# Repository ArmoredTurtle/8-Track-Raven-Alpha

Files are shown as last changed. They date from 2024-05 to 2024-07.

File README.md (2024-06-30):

8-Track Raven 4 spool automated filament changer.

V0.0.41

Join our discord server here:

Join me on Discord (https://discord.gg/eT8zc3bvPR)

## Intro

This is an alpha version of the 8-Track project.
8-Track is a modular automated filament changer that is scaleable and compatible with any KLIPPER 3d printer.
Specifically 8-Track Raven's purpose is to do public testing of critical components at a lower price point.
Raven retains the same cassettes as the 8-Track while simplifying the hub and uses an off the shelf MCU.

## Objectives
The goal of alpha testing this project is to refine the cassettes as much as possible and prove reliability of the system.
Features like active filament drying are being worked on but do not currently have a timeline.

## Compatibility
Almost everything is subject to change unless specified as set in stone such as:
Cassette dimensions, 8-Track Raven frame.

# Raven BOM (Bill of Materials)

## Frame
| Qty | Item |
|-----|---|
| 4 | 412.5 2020 extrusions |
| 2 | 304.5 2020 extrusions |
| 2 | 219mm extrusions |
| 8 | M5x25 BHCS |
| 2 | M5x8 BHCS |
| 2 | M5 Roll Nuts |

## Hardware
| Qty | Item |
|-----|---|
| 4 | B-side cassete PCBs |
| 56  | M3x5 Heat set inserts |
| 16  | 0.5x5x15 Coil Springs |
| 16  | M3x20 FHCS |
| 32  | M3x12 SHCS |
| 32  | M5 Roll nuts |
| 32  | M5x10 BHCS |
| 11  | ECAS04 (remove rubber spacer) |

## Printed Parts
| Qty | Part Name |
|---|---|
| 1 - 4  | Backer_X |
| 4 | Backer_PCB_Spring_Plate_x4 |
| 1-4 | Drop_Plate_X |
| 1 | Mid_Plate_Lower |
| 1 | Mid_Plate_Upper |
| 1 | 6-1_Hub |
| 1 | BTT_MMB_CAN_Mount |

# Cassette BOM ((Bill of Materials)  Per Cassette)

## Electronics
| Qty | Item |
|-----|---|
| 1 | 20mm Nema 17 motor |
| 1 | Endstop microswitch (Omron D2F) |
| 1 | mg 996r servo |
| 1 | Cassette Side-A PCB |

## Hardware
|  Qty  | Item |
|---|---|
|  21 | M3x6 SHCS |
|  6 | M3x8 SHCS |
|  7 | M3x20 SHCS |
|  3 | M3x20 FHCS |
|  6 | M3 Washer |
|  20 | M3x5 Heat set inserts |
|  1 | BMG Extruder gear kit |
|  1 | Spring (6mm OD, 1mm Wire Size, 7.5mm Compressed Length, 15mm Free Length, 37.2N Load Capacity) |
|  2 | #211 Orings (13/16" ID, 1 1/16" OD) |
|  4 | 608 Bearings |
|  1 | R4zz Bearing OR 634ZZ (print tension arms) |
|  2 | 80x8mm Shaft |
|  1 | HF081412 one way bearing (8mm ID, 14mm OD, 12mm L) |
|  1 | 5mm Steel ball bearing |
| ~32mm | 4mm OD 3mm ID bowden tube |
|  4 | 6x3mm magnets |
|  1 | 0.5x5x15 Coil Spring |
| *** | If split cassette +1 M3x6 SHCS, +1 M3X5 heat set insert |

## Printed Parts
| Qty | Item |
|-----|---|
| 1 | Cassette Lid |
| 1 | Cassette Shell |
| 1 | Frane |
| 1 | Idler Frame |
| 1 | TensionArm_Upper |
| 1 | TensionArm_Lower |
| 2 | Idler Roller |
| 2 | Idler Spacer |
| 2 | Inner Roller |
| 2 | Roller_TPU95A |

*Insert lots more reading material here *later**

[Buy me a coffee to help keep this project going!](https://buymeacoffee.com/armoredturtle)

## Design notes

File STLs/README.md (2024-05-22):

# Print Settings
All parts should be printed in these settings unless specifically called out here as otherwise.

| Setting 	| Value 	|
|---	|---	|
| Nozzle 	| 0.4mm 	|
| Layer Height 	| 0.2mm 	|
| Perimeters/Walls 	| 4 	|
| Bottom Layers 	| 4 	|
| Top Layers 	| 4 (0.8mm) 	|
| Infil Density 	| 15 	|
| Infil Pattern 	| Gyroid 	|

## Material choice
PLA, PETG and ABS have been tested, all work however PETG is not recommended for extruder parts or drop plates.
When using heated inserts, be sure to use appropriate temperatures for your selected material.

## Part call out!
Guidler: same settings with 6 perimeters and 40% infill

Servo_Arm: Same as guidler unless pla. If in PLA print at 100% infill.

6-1Hub: Increase infill to 20% to ensure proper support of filament paths.

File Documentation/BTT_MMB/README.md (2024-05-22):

# BTT MMB CAN Board

Full information on the BTT MMB CAN board can be found here:
https://github.com/bigtreetech/MMB

# Details
This project requires use of four independently controllable servo motors.

When controlling these via an STM32 or similar micro controller, it is mandatory to use an ADC pin.

There are four accessible ADC pins on this board:

PA0 PA1 PA3 PA4

These will be used in the config for the servos. If you use a different pin your servo will not work.

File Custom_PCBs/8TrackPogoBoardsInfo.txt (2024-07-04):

The 5V port on these boards is intended for future shenanigans and does not need to be hooked to anything.
It is common to the 5V and GND going to the servo.

Identification: There is A-Side and B-Side, you can identify this by the side that the JST connectors are on, not the side that the pogo is on.
B-side boards have the male pogos and go on your hub (raven or other) A-side boards have the female pogos and are for the cassettes. 

The pogo pins can be sourced here, you want the 8-pin NO EAR variation.
https://www.aliexpress.us/item/3256805938998871.html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
Each pair uses 2 4 pin JST-XH connectors, 2 3 pin, 4 2 pin.

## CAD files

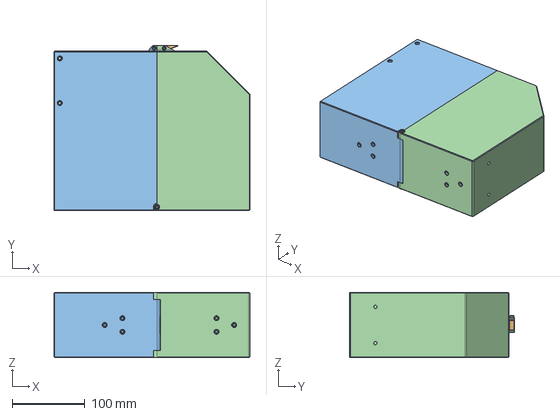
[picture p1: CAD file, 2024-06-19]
CAD/Split_Cassette_Bottom_Hinge v2.step
270.1 x 228.0 x 90.0 mm
M3x20 SHCS x 4

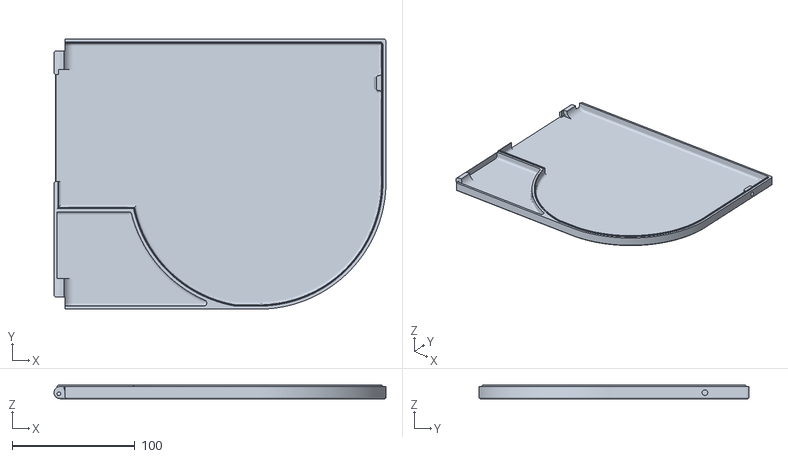
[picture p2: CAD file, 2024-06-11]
STLs/Cassette/Cassette_Lid.stl
270.2 x 220.0 x 11.0

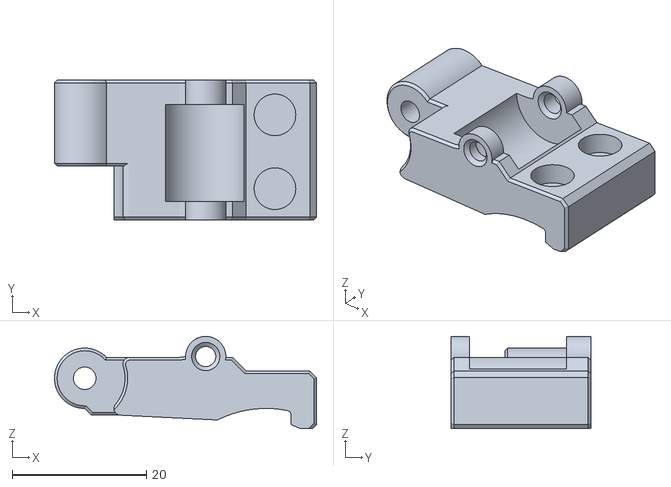
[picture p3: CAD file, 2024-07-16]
STLs/Cassette/Extruder_Module_V2/Thickened Guidler.stl
39.0 x 20.8 x 13.7

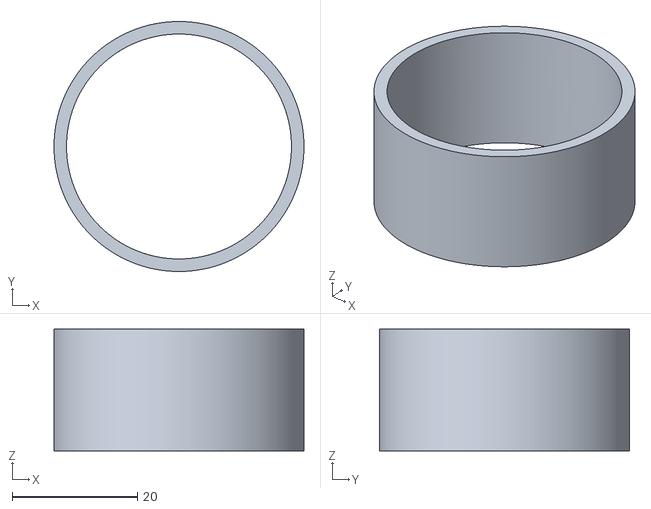
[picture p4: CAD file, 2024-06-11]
STLs/Cassette/Respooler/Roller_TPU95A_x2.stl
39.8 x 39.8 x 19.4

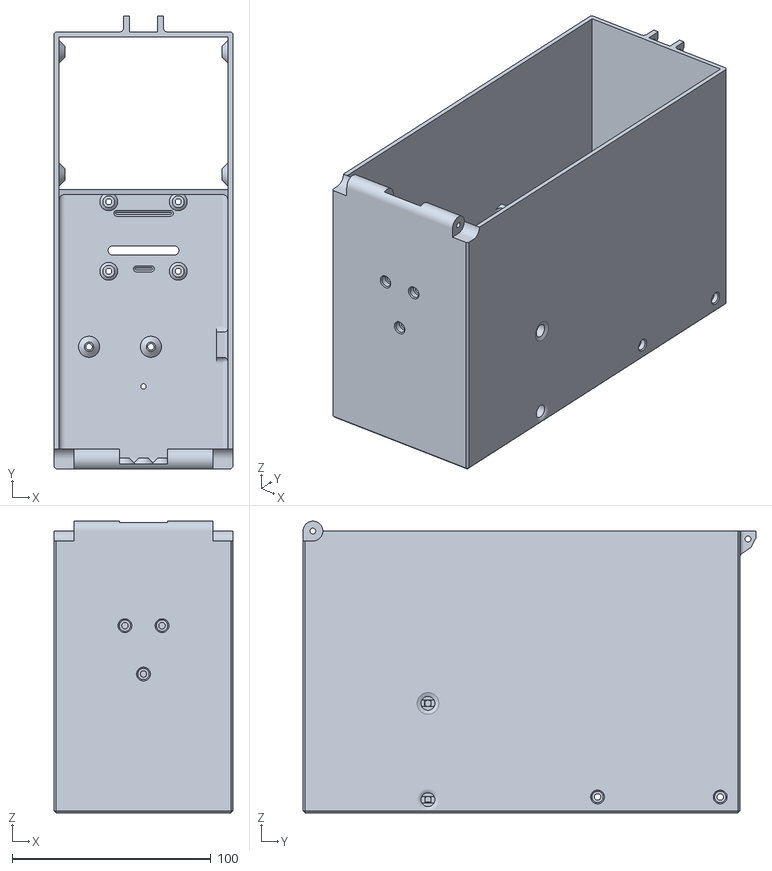
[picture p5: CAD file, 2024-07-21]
STLs/Cassette/Split_Cassette/Split_Cassette_L.stl
90.0 x 228.0 x 146.8

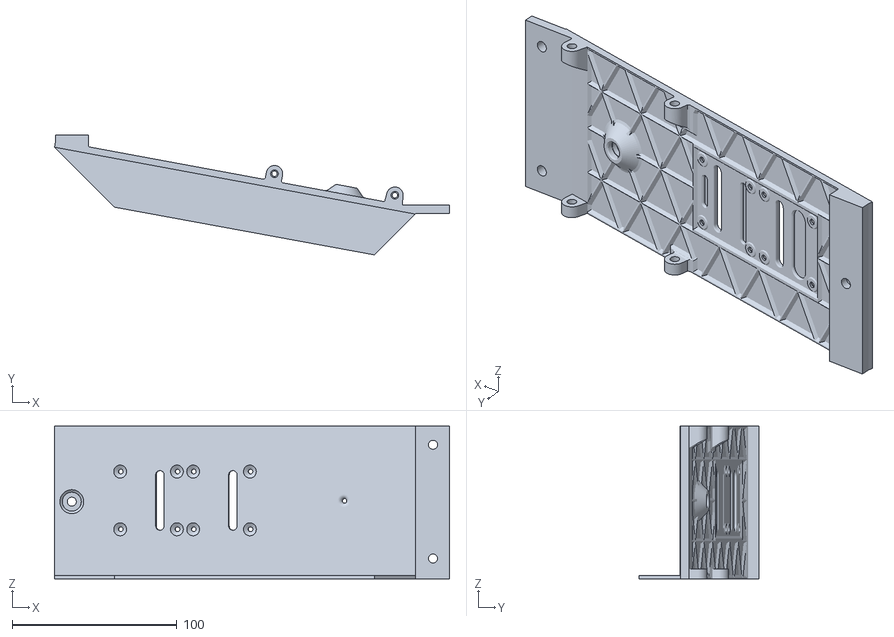
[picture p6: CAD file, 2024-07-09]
STLs/Raven_Parts/Backer_3.stl
239.5 x 72.6 x 92.5

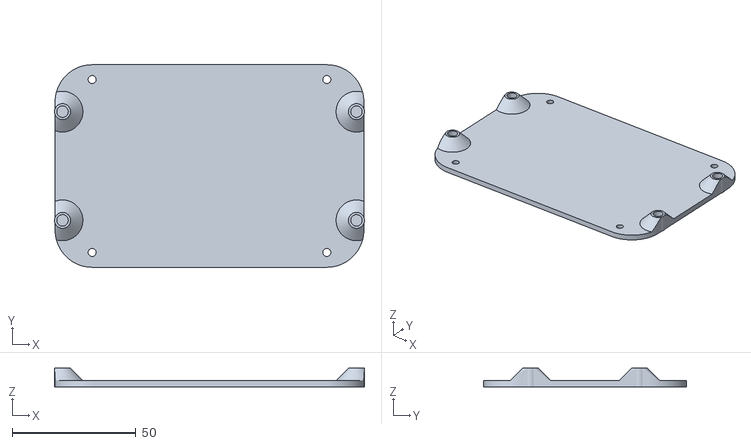
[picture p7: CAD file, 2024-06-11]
STLs/Raven_Parts/Electronics/BTT_MMB_CAN_Mount.stl
125.5 x 82.0 x 7.50

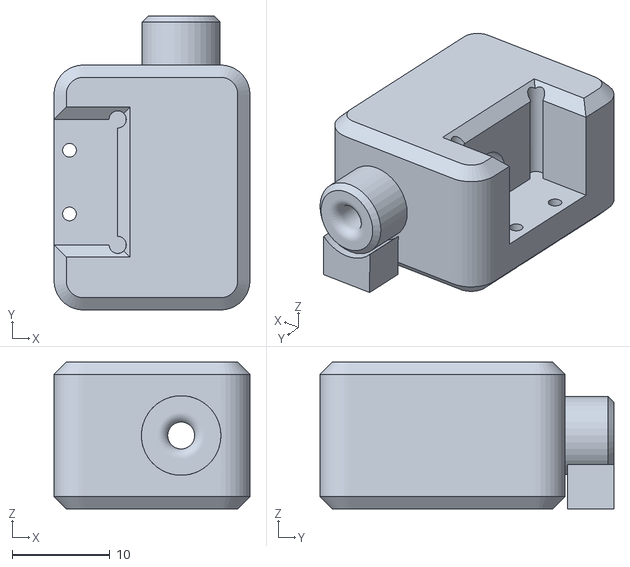
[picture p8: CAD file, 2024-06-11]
STLs/Raven_Parts/FilamentPath/FilaTector_V2.stl
20.0 x 30.0 x 15.0

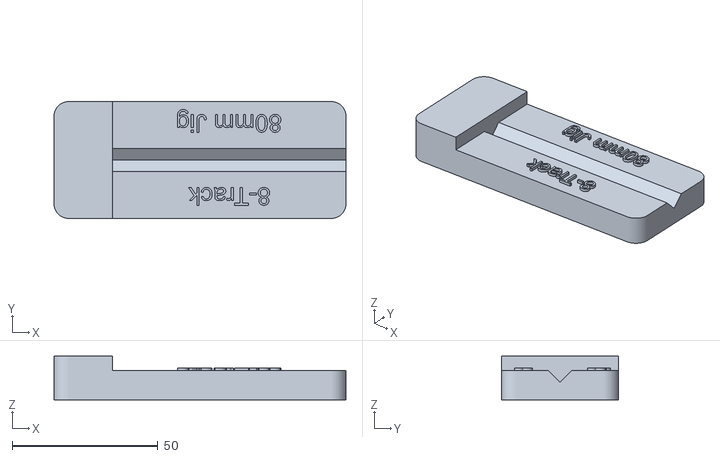
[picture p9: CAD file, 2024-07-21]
STLs/Tools/8-Track-80mm-Jig.stl
100.0 x 40.0 x 15.0

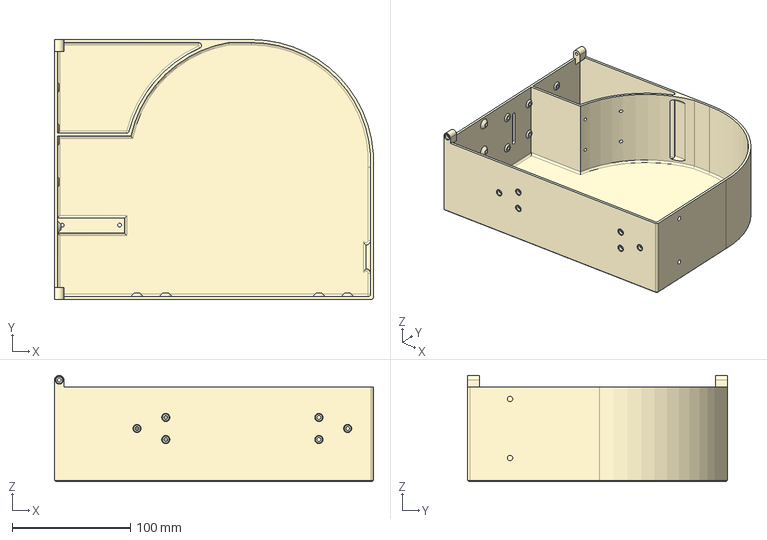
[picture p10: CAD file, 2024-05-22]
CAD/Cassette_Shell.step
270.1 x 220.0 x 90.0 mm

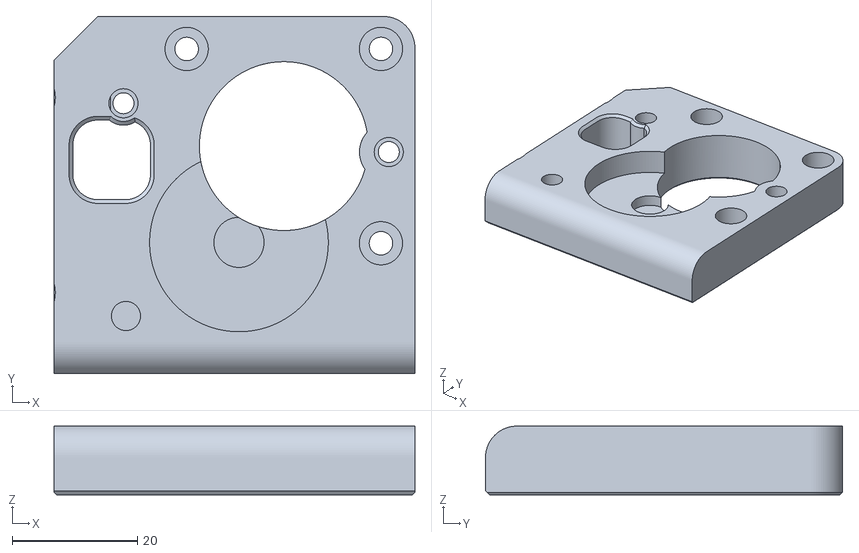
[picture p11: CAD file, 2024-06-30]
STLs/Cassette/Extruder_Module_V2/Extruder_Body.stl
57.6 x 56.9 x 11.0

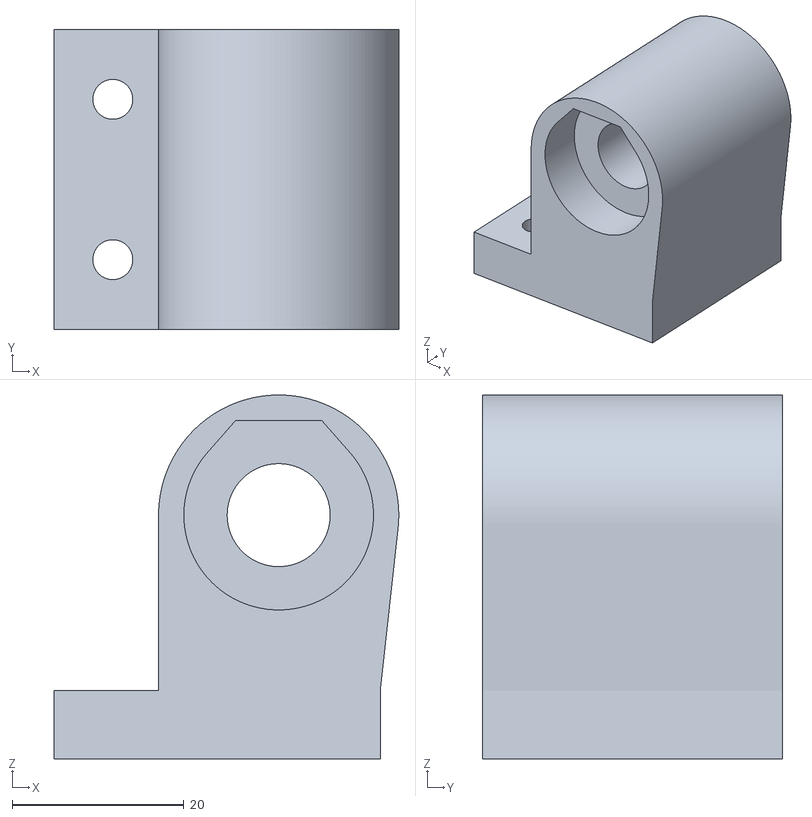
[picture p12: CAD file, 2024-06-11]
STLs/Cassette/Respooler/Idler_Frame.stl
40.2 x 35.0 x 42.4

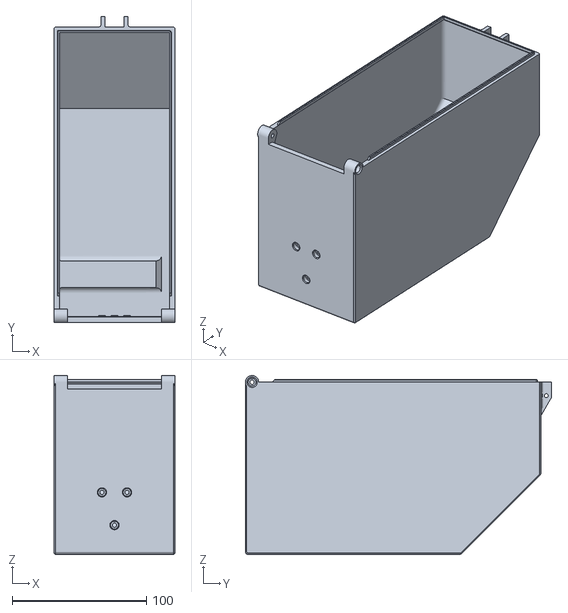
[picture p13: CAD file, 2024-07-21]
STLs/Cassette/Split_Cassette/Split_Cassette_U.stl
90.0 x 228.0 x 133.2

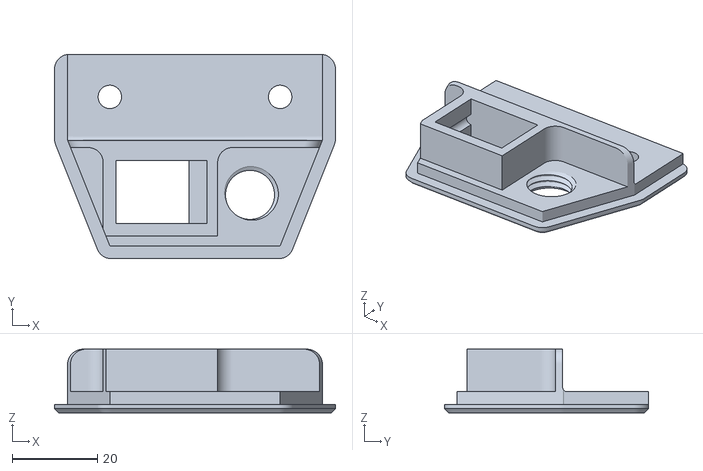
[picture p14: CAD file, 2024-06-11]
STLs/Raven_Parts/Electronics/PG7_Keystone.stl
66.0 x 48.0 x 15.0

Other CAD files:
STLs/Raven_Parts/Backer_1.stl
STLs/Cassette/Extruder_Module_V2/Guidler.stl
STLs/Cassette/Respooler/Inner_Roller_x2.stl
STLs/Cassette/Split_Cassette/Latch.stl
STLs/Cassette/Extruder_Module_V2/Extruder_Hat.stl
STLs/Cassette/Extruder_Module_V2/Extruder_Hat_Flared.stl
STLs/Cassette/Extruder_Module_V2/Microswitch_Lock.stl
STLs/Cassette/Extruder_Module_V2/Saver_Arm.stl
STLs/Cassette/Extruder_Module_V2/Servo_Saver.stl
STLs/Cassette/Respooler/Center_Drive_Roller.stl
STLs/Cassette/Respooler/Frame.stl
STLs/Cassette/Respooler/Idler_Roller_x2.stl
STLs/Cassette/Respooler/Idler_Spacer_x2.stl
STLs/Cassette/Respooler/TensionerArm_Lower_634ZZ.stl
STLs/Cassette/Respooler/TensionerArm_Lower_R4ZZ.stl
STLs/Cassette/Respooler/TensionerArm_Upper_634ZZ.stl
STLs/Cassette/Respooler/TensionerArm_Upper_R4ZZ.stl
STLs/Raven_Parts/Backer_2.stl
STLs/Raven_Parts/Backer_4.stl
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

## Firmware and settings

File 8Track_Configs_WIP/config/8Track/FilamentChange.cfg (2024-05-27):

[gcode_macro T0]
gcode:
    _CHANGE_TOOL TOOL="cas1"

[gcode_macro T1]
gcode:
   _CHANGE_TOOL TOOL="cas2"
   
[gcode_macro T2]
gcode:
    _CHANGE_TOOL TOOL="cas3"

[gcode_macro T3]
gcode:
   _CHANGE_TOOL TOOL="cas4"

[gcode_macro Zero_Servos]
gcode:
  SET_SERVO SERVO=cas1 ANGLE={printer["gcode_macro _MMU_VAR"].servo_up_angle}
  SET_SERVO SERVO=cas2 ANGLE={printer["gcode_macro _MMU_VAR"].servo_up_angle}
  SET_SERVO SERVO=cas3 ANGLE={printer["gcode_macro _MMU_VAR"].servo_up_angle}
  SET_SERVO SERVO=cas4 ANGLE={printer["gcode_macro _MMU_VAR"].servo_up_angle}

  MANUAL_STEPPER STEPPER=cas1 ENABLE=0
  MANUAL_STEPPER STEPPER=cas2 ENABLE=0
  MANUAL_STEPPER STEPPER=cas3 ENABLE=0
  MANUAL_STEPPER STEPPER=cas4 ENABLE=0
   
[gcode_macro CLEAR]
gcode:
  SAVE_VARIABLE VARIABLE=hub_loaded value="'unloaded'"
  SAVE_VARIABLE VARIABLE=tool_loaded value="'unloaded'"
  SAVE_VARIABLE VARIABLE=current_load VALUE="'cas0'"

[gcode_macro BRUSH]
gcode:
 G1 X85 Y350 F15000
 {% set brush = 0 %}
 {% for brush in range(3) %}
   G1 X85 Y350 Z3 F12000
   G1 X115 Y350 Z3 F12000
 {% endfor %}

[gcode_macro _Track_Check_Extruder_Load]
gcode:
  {% if printer['filament_switch_sensor tool'].filament_detected is sameas true %}
      SAVE_VARIABLE VARIABLE=current_load VALUE="'{params.CASEX}'"
      {% if printer.save_variables.variables.tool_loaded == "unloaded" %}
        MANUAL_STEPPER STEPPER={params.CASEX} MOVE=55 SPEED=5 SET_POSITION=0 SYNC=0
        M83
        G1 E55 F300
        MANUAL_STEPPER STEPPER={params.CASEX} SYNC=1
        SAVE_VARIABLE VARIABLE=tool_loaded value="'loaded'"
    {% endif %}
  {% else %}
      MANUAL_STEPPER STEPPER={params.CASEX} MOVE=15 SPEED=5 SET_POSITION=0 #SYNC=0
      #M83
      #G1 E15 F300
      #MANUAL_STEPPER STEPPER={params.CASEX} SYNC=1
  {% endif %}   
    
[gcode_macro Tool_Load]
gcode:
  {% set choiceS = params.CAS|default(cas1) %}
  SET_SERVO SERVO={choiceS} ANGLE={printer["gcode_macro _MMU_VAR"].servo_down_angle}
  MANUAL_STEPPER STEPPER={choiceS} MOVE={printer["gcode_macro _MMU_VAR"].min_bowden_length} SPEED=150 ACCEL=50 SET_POSITION=0 SYNC=0
  {% set step = 0 %}
  {% for step in range(printer["gcode_macro _MMU_VAR"].loop_count) %}
    _Track_Check_Extruder_Load CASEX={choiceS}
  {% endfor %}
  MANUAL_STEPPER STEPPER={choiceS} ENABLE=0
  SET_SERVO SERVO={choiceS} ANGLE={printer["gcode_macro _MMU_VAR"].servo_up_angle}
  {% if printer["gcode_macro _MMU_VAR"].wipe > 0 %}
    BRUSH
  {% endif %}
  {% if printer["gcode_macro _MMU_VAR"].filament_poop > 0 %}
    _POOP
  {% endif %}

[gcode_macro _CHANGE_TOOL]
gcode:
  {% set SELTOOL = params.TOOL|default(cas1) %}
  {% set UnloadTool = printer.save_variables.variables.current_load %}
  {% if printer.save_variables.variables.current_load == SELTOOL %}
  {% else %}
    {% if printer.save_variables.variables.tool_loaded == "loaded" %}
      {% if printer["gcode_macro _MMU_VAR"].filament_cut > 0 %}
       M83
       G1 E-10 F300
       {% set cutZ = printer.toolhead.position.z+5 %}
       {% set cut = 0 %}
       {% for cut in range(2) %}
        G1 X{printer["gcode_macro _MMU_VAR"].X_pos_cut} Y{printer["gcode_macro _MMU_VAR"].Y_pos_cut} Z{cutZ} F10000
        G1 X0 F1000
       {% endfor %}
      {% endif %}
      {% if printer["gcode_macro _MMU_VAR"].park > 0 %}
       _TOOL_PARK
      {% endif %}
      {% if printer["gcode_macro _MMU_VAR"].filament_form_tip > 0 %}
        _FORM_TIP
      {% endif %}
      SET_SERVO SERVO={UnloadTool} ANGLE={printer["gcode_macro _MMU_VAR"].servo_down_angle}
      MANUAL_STEPPER STEPPER={UnloadTool} MOVE={printer["gcode_macro _MMU_VAR"].sensor_to_nozzle * -1} SPEED=20 SET_POSITION=0 SYNC=0
      M83
      G1 E{printer["gcode_macro _MMU_VAR"].sensor_to_nozzle * -1} F1200
      MANUAL_STEPPER STEPPER={UnloadTool} SYNC=1
      MANUAL_STEPPER STEPPER={UnloadTool} MOVE={printer["gcode_macro _MMU_VAR"].min_bowden_length * -1} SPEED=150 ACCEL=50 SET_POSITION=0
      MANUAL_STEPPER STEPPER={UnloadTool} ENABLE=0
      SET_SERVO SERVO={UnloadTool} ANGLE={printer["gcode_macro _MMU_VAR"].servo_up_angle}
      SAVE_VARIABLE VARIABLE=current_load VALUE="'cas0'"
      SAVE_VARIABLE VARIABLE=tool_loaded value="'unloaded'"
      Tool_Load CAS={SELTOOL}
    {% else %}
      {% if printer["gcode_macro _MMU_VAR"].park > 0 %}
       _TOOL_PARK
      {% endif %}
      Tool_Load CAS={SELTOOL}
    {% endif %} 
  {% endif %} 
  
[gcode_macro _TOOL_PARK]
gcode:
  G1 X{printer["gcode_macro _MMU_VAR"].x_pos_change} Y{printer["gcode_macro _MMU_VAR"].y_pos_change} F10000
  G1 Z{printer["gcode_macro _MMU_VAR"].z_pos_change} F1000

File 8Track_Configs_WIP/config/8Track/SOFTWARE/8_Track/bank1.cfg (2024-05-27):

[mcu BANK1]
canbus_uuid=be66b54fe6f2

[temperature_sensor Bank_1]
sensor_type: temperature_mcu
sensor_mcu: BANK1

[servo cas1]
pin:  BANK1:PA0
maximum_servo_angle: 65
minimum_pulse_width: 0.00085
maximum_pulse_width: 0.00215

[servo cas3]
pin:  BANK1:PA1
maximum_servo_angle: 65
minimum_pulse_width: 0.00085
maximum_pulse_width: 0.00215

[servo cas5]
pin: BANK1:PA3
maximum_servo_angle: 40
minimum_pulse_width: 0.00085
maximum_pulse_width: 0.00215

[servo cas7]
pin:  BANK1:PA4
maximum_servo_angle: 65
minimum_pulse_width: 0.00085
maximum_pulse_width: 0.00215

[manual_stepper cas1]
step_pin: BANK1:PB15
dir_pin: BANK1:PB14
enable_pin: !BANK1:PA8
microsteps: 16
rotation_distance: 22.9816

[tmc2209 manual_stepper cas1]
uart_pin: BANK1:PA10
uart_address: 0
run_current: .8
hold_current: 0.4

[manual_stepper cas3]
step_pin: BANK1:PD2
dir_pin: !BANK1:PB13
enable_pin: !BANK1:PD1
microsteps: 16
rotation_distance: 7.84922

[tmc2209 manual_stepper cas3]
uart_pin: BANK1:PC7
uart_address: 0
run_current: 1
hold_current: 0.4

[manual_stepper cas5]
step_pin: BANK1:PD0
dir_pin: !BANK1:PD3
enable_pin: !BANK1:PA15
microsteps: 16
rotation_distance: 7.84922

[tmc2209 manual_stepper cas5]
uart_pin: BANK1:PC6
uart_address: 0
run_current: 1
hold_current: 0.4

[manual_stepper cas7]
step_pin: BANK1:PB6
dir_pin: BANK1:PB7
enable_pin: !BANK1:PB5
microsteps: 16
rotation_distance: 22.9816

[tmc2209 manual_stepper cas7]
uart_pin: BANK1:PA9
uart_address: 0
run_current: .8
hold_current: 0.4

#[filament_switch_sensor cas1]
#switch_pin: BANK1:PB9
#pause_on_runout: False

#[filament_switch_sensor cas3]
#switch_pin: BANK1:PC15
#pause_on_runout: False

#[filament_switch_sensor cas5]
#switch_pin: BANK1:PC14
#pause_on_runout: False

#[filament_switch_sensor cas7]
#switch_pin: BANK1:PB11
#pause_on_runout: False

#[filament_switch_sensor slot1]
#switch_pin: BANK1:PB2

#[filament_switch_sensor slot3]
#switch_pin: BANK1:PC13

#[filament_switch_sensor slot5]
#switch_pin: BANK1:PB12

#[filament_switch_sensor slot7]
#switch_pin: BANK1:PB10

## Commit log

2024-05-23 Add files via upload
    fixed an issue with the respooler frame model rubbing the drive roller
    [Frame.stl]
2024-05-24 fix: update respooler BOM
2024-05-30 Extruder Hat with filament switch
    [Extruder_Hat.stl]
2024-05-30 Delete CAD/Raven_Assembled v10.step
    updated to v11
2024-06-04 Add files via upload
    new respooler parts
    [TensionArm_Upper.stl, TensionerArm_Lower.stl]
2024-06-04 Update README.md
    Updated Cassette BOM to be complete and accurate
2024-06-18 Remove older Center Drive Roller
    [Center Drive Roller.stl]
2024-06-18 Remove Idler_Roller_X2.stl
    [Idler_Roller_X2.stl]
2024-06-30 Delete STLs/Cassette/Extruder directory
    Updated extruder module to V2
    [Extruder_Body.stl, Extruder_Hat.stl, Guidler.stl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]
2024-07-09 Fixed alignment issue with backer filament path. Fixed a couple print issues on split cassette. - Added chamfer to internal overhang - Added bridging to extruder mount screw holes Fixed alignment iss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
    [Backer_1.stl, Backer_2.stl, Backer_3.stl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]
2024-07-09 Standardize file naming
    [BTT_MMB_CAN_Mount.stl, Backer_1.stl, Backer_2.stl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]
2024-07-21 Delete CAD/Raven_Assembled_Hardware v29.zip
    update to v34
